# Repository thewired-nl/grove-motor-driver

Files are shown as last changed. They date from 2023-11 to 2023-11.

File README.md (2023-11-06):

# Grove-compatible Motor Driver TB6612
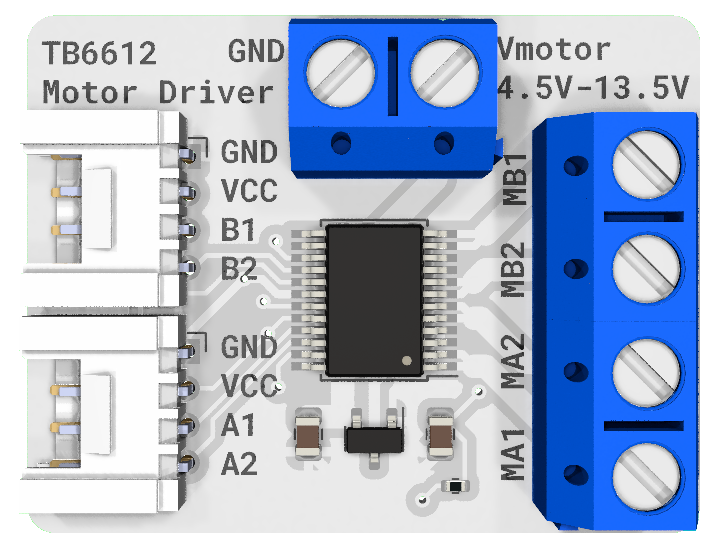
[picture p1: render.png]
3D render of the PCB


Circuit based on the [Adafruit breakout board](https://www.adafruit.com/product/2448) with the same chip, but with a Grove connector per motor channel and screw terminals for ease of use.
Datasheet: [TB6612FNG](https://cdn-shop.adafruit.com/datasheets/TB6612FNG_datasheet_en_20121101.pdf)

| Specs | |
| --- | --- |
| Motor voltage | 4.5 - 13.5v |
| Max amperage (per motor) | 1.2A (3.2A peak) |

This motor driver features 2 outputs (A and B), which can be individually controlled through their respective Grove connector.
Suitable for basic motors, linear actuators and solenoids.

# Wiring
Connect an external power supply between 4.5 - 13.v volts to the top screw terminal. Make sure ground is on the left (GND). Motor(s) can be connected to the outputs for Motor A (MA1, MA2) and/or Motor B (MB1, MB2) screw terminals. You can connect your motor wires either way, this only influences which throttle values will be forward/backward.

## Software
For use with CircuitPython, the [Adafruit motor library](https://docs.circuitpython.org/projects/motor/en/latest/index.html#) works quite well:

```python
import time
import board
import pwmio
import adafruit_motor

# One Grove port is used per motor output, make sure they don't have pin overlap
# TODO: figure out best PWM frequency

# A1, A2 Grove port connected to ItsyBitsy Expander port D2
pwmA1 = pwmio.PWMOut(board.D2, duty_cycle=0, frequency=5000)
pwmA2 = pwmio.PWMOut(board.D3, duty_cycle=0, frequency=5000)

# B1, B2 Grove port connected to ItsyBitsy Expander port D4
pwmB1 = pwmio.PWMOut(board.D4, duty_cycle=0, frequency=5000)
pwmB2 = pwmio.PWMOut(board.D7, duty_cycle=0, frequency=5000)

motorA = adafruit_motor.motor.DCMotor(pwmA1, pwmA2)
motorB = adafruit_motor.motor.DCMotor(pwmB1, pwmB2)

while True:
  # throttle ranges from -1.0 (full speed reverse) to 1.0 (full speed forward)
  motorA.throttle = 1
  motorB.throttle = 0
  time.sleep(2)
  motorA.throttle = -0.5
  motorB.throttle = -0.5
  time.sleep(2)
  motorA.throttle = 0
  motorB.throttle = 1
  time.sleep(2)
```

## License
[Creative Commons BY-SA 4.0](https://creativecommons.org/licenses/by-sa/4.0/)

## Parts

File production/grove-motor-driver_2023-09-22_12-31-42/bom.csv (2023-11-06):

Designator | Footprint | Quantity | Value | LCSC Part #
C5, C6 | 0805 | 2 | 10uF | C15850
J10 | PinHeader_1x04_P2.00mm_Horizontal | 1 | Grove Motor 1
J11, J12 | DG301-5.0-2P-1X | 2 | Screw_Terminal_01x02
J13 | PinHeader_1x04_P2.00mm_Horizontal | 1 | Grove Motor 2
J9 | DG301-5.0-2P-1X | 1 | VMOTORIN
JP1, JP2 | SolderJumper-2_P1.3mm_Bridged_Pad1.0x1.5mm | 2 | SolderJumper_2_Bridged
Q1 | SOT-23 | 1 | Q_PMOS_GSD | C96616
R9 | 0402 | 1 | 10K | C25744
U2 | SSOP-24_5.3x8.2mm_P0.65mm | 1 | TB6612FNG | C88224

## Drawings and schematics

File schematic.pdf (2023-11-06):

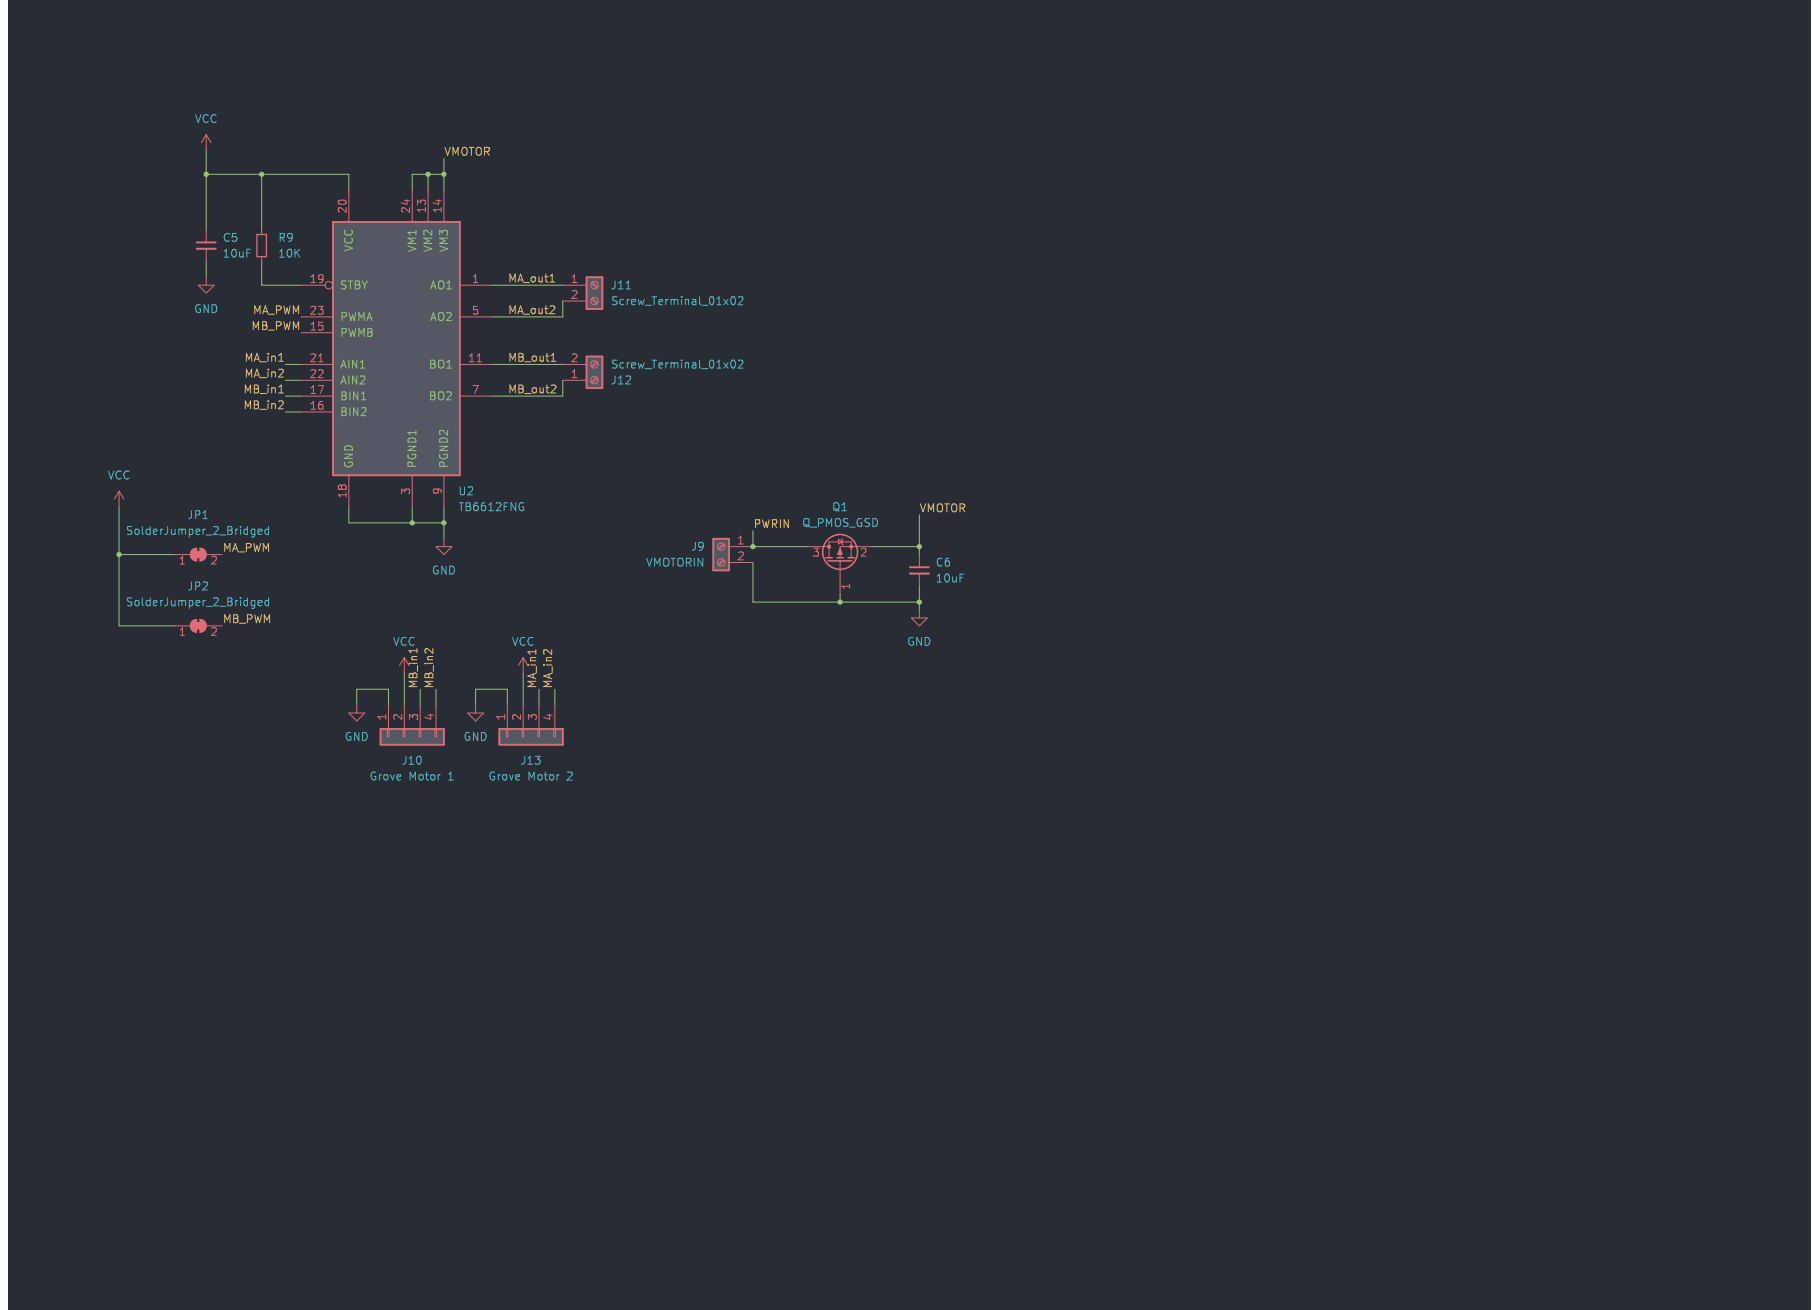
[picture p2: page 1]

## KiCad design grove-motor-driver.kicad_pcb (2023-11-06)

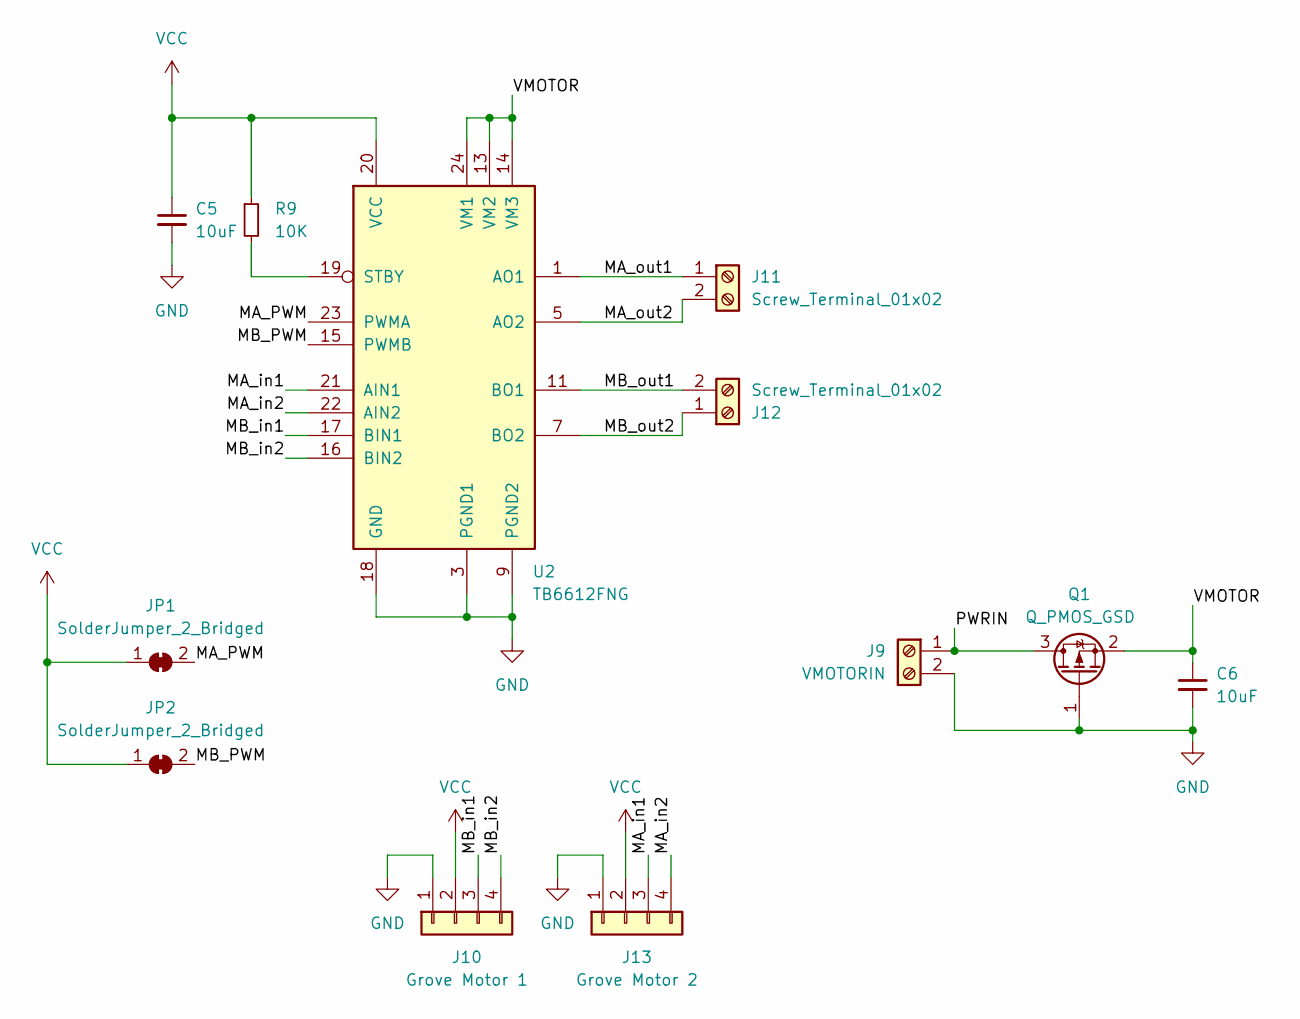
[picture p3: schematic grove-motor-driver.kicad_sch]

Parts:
C5, C6: 10uF; C_0805_2012Metric; MPN C15850
J9: VMOTORIN; DG301-5.0-2P-1X
J10: Grove Motor 1; GroveHorizontal
J11, J12: Screw_Terminal_01x02; DG301-5.0-2P-1X
J13: Grove Motor 2; GroveHorizontal
JP1, JP2: SolderJumper_2_Bridged; SolderJumper-2_P1.3mm_Bridged_Pad1.0x1.5mm
Q1: Q_PMOS_GSD; SOT-23; MPN C96616
R9: 10K; R_0402_1005Metric; MPN C25744
U2: TB6612FNG; SSOP-24_5.3x8.2mm_P0.65mm; MPN C88224

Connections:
/MA_PWM: JP1.2 (B), U2.23 (PWMA)
/MA_in1: J13.3, U2.21 (AIN1)
/MA_in2: J13.4, U2.22 (AIN2)
/MA_out1: J11.1, U2.1 (AO1), U2.2 (AO1)
/MA_out2: J11.2, U2.5 (AO2), U2.6 (AO2)
/MB_PWM: JP2.2 (B), U2.15 (PWMB)
/MB_in1: J10.3, U2.17 (BIN1)
/MB_in2: J10.4, U2.16 (BIN2)
/MB_out1: J12.2, U2.11 (BO1), U2.12 (BO1)
/MB_out2: J12.1, U2.7 (BO2), U2.8 (BO2)
/PWRIN: J9.1, Q1.3 (D)
/VMOTOR: C6.1, Q1.2 (S), U2.13 (VM2), U2.14 (VM3), U2.24 (VM1)
GND: C5.2, C6.2, J9.2, J10.1, J13.1, Q1.1 (G), U2.3 (PGND1), U2.4 (PGND1), U2.9 (PGND2), U2.10 (PGND2), U2.18 (GND)
unnamed: R9.2, U2.19 (STBY)
VCC: C5.1, J10.2, J13.2, JP1.1 (A), JP2.1 (A), R9.1, U2.20 (VCC)

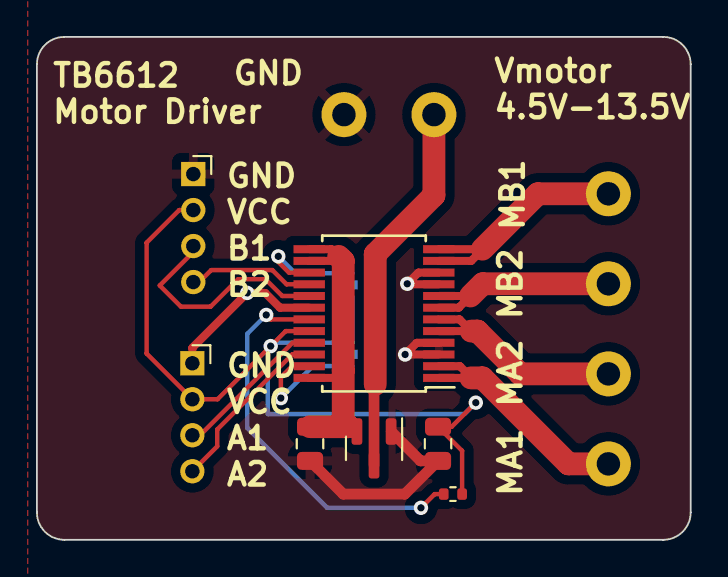
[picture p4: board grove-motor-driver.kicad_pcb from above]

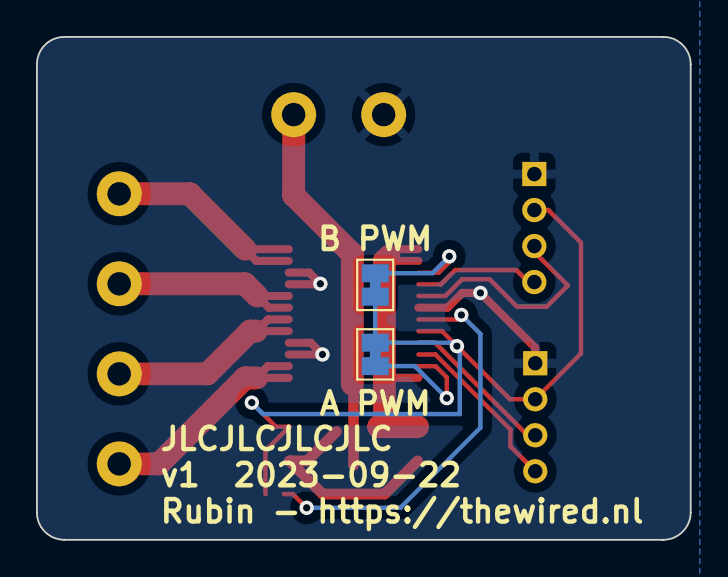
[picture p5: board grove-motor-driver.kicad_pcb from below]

Board: 2 copper layers, 36.3 x 27.9 mm, 12 parts (2 on the bottom side), 15 nets.
